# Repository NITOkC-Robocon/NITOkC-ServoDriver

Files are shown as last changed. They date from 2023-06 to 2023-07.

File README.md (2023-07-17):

# NITOkC-ServoDriver

## 概要
弊部独自のサーボドライバの回路データ、およびプログラムです<br>
(※デフォルトブランチ：main)

## 機能
- 2セルLiPoバッテリーからの給電
  - マイコンへの給電(電源切り離し機能付き)
  - サーボへの給電(レギュレータにより6Vに降圧)
- 中点指定機能
- 出力選択機能
- PWM幅可変機能
- 外部入力機能
  - 基板上のスライドスイッチによって切り替え可能

## 環境
| | |
| :-: | --- |
| OS | Windows 10 Pro |
| プログラム | Arm Keil Studio |
| 基板作成 | KiCad 7.0 |
| 使用マイコン | NUCLEO-F303K8 |
| 使用言語 | C++ |
| その他 | 弊部独自ライブラリの導入が必須(Privateリポジトリのため、今後依存関係を解消予定) |

## 開発者
[Resenaga_Byakko (Shogo Miyazato)](https://github.com/ByakkoMatsumiya)

## 連絡先
基板またはコードに関するお問い合わせは、[Issues](https://github.com/NITOkC-Robocon/NITOC-Robocon_HP/issues)または下記連絡先へお願い致します。
- [Twitter | @Seyanaga (趣味用アカウント)](https://twitter.com/Seyanaga)
- [Twitter | @Myaaaazato (ロボコン用アカウント)](https://twitter.com/Myaaaazato)

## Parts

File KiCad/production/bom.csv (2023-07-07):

Designator | Footprint | Quantity | Value | LCSC Part #
C1, C4 | CP_Radial_D8.0mm_P3.50mm | 2 | 100u
C2 | C_Disc_D3.4mm_W2.1mm_P2.50mm | 1 | 0.33u
C3 | C_Disc_D4.3mm_W1.9mm_P5.00mm | 1 | 0.1u
D1, D2 | D_DO-15_P10.16mm_Horizontal | 2 | PS2010R
D3 | LED_D3.0mm | 1 | SLR-332VC3F
D4 | LED_D3.0mm | 1 | SLR-332MC3F
D5 | LED_D3.0mm | 1 | SLR-332DC3F
D6 | LED_D3.0mm | 1 | SLR-332YC3F
J1 | Connector_T_Male | 1 | 2Cell
J2 | PinHeader_1x03_P2.54mm_Vertical | 1 | Servo_1
J3 | PinHeader_1x03_P2.54mm_Vertical | 1 | Servo_2
J4 | PinHeader_1x03_P2.54mm_Vertical | 1 | SIGNAL_INPUT
JP1 | PinHeader_1x02_P2.54mm_Vertical | 1 | VIN_BATT
R1, R2 | R_Axial_DIN0207_L6.3mm_D2.5mm_P10.16mm_Horizontal | 2 | 680
R3, R4, R5 | R_Axial_DIN0207_L6.3mm_D2.5mm_P10.16mm_Horizontal | 3 | 100
RV1 | Potentiometer_Alps_RK09K_Single_Vertical | 1 | 10k_B
SW1 | Slide_SS12D01Gx | 1 | PWM1_SW
SW2 | Slide_SS12D01Gx | 1 | PWM2_SW
SW3 | SW_PUSH_6mm | 1 | RST_SW
SW4 | SW_PUSH_6mm | 1 | CENTER_SW
SW5 | SW_PUSH_6mm | 1 | EN1_SW
SW6 | SW_PUSH_6mm | 1 | EN2_SW
U1 | TO-220-3_Vertical | 1 | LM7806_TO220
U2 | NUCLEO F303 K8 | 1 | NUCLEO_F303K8

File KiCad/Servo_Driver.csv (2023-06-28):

Source: | C:\Users\ic201239\Documents\KiCad\Servo_Controller\Servo_Controller.kicad_sch
Date: | 2023/05/24 18:18:11
Tool: | Eeschema 7.0.2
Generator: | C:\Program Files\KiCad\7.0\bin\scripting\plugins/bom_csv_grouped_by_value_with_fp.py
Component Count: | 29
Ref | Qnty | Value | Cmp name | Footprint | Description | Vendor | DNP
C1, C5 | 2 | 100u | C_Polarized_Small |  | Polarized capacitor, small symbol
C2, C4, C6, C7 | 4 | 0.1u | C_Small |  | Unpolarized capacitor, small symbol
C3 | 1 | 0.33u | C_Small |  | Unpolarized capacitor, small symbol
D1 | 1 | SLR-332VC3F | LED |  | Light emitting diode
D2 | 1 | SLR-332MC3F | LED |  | Light emitting diode
D3 | 1 | SLR-332DC3F | LED |  | Light emitting diode
D4 | 1 | SLR-332YC3F | LED |  | Light emitting diode
J1 | 1 | 2Cell | Conn_01x02_Pin |  | Generic connector, single row, 01x02, script generated
J2 | 1 | Servo_1 | Conn_01x03_Pin |  | Generic connector, single row, 01x03, script generated
J3 | 1 | Servo_2 | Conn_01x03_Pin |  | Generic connector, single row, 01x03, script generated
J4 | 1 | SIGNAL_INPUT | Conn_01x03_Pin |  | Generic connector, single row, 01x03, script generated
R1, R2 | 2 | 640 | R |  | Resistor
R3, R4, R5 | 3 | 100 | R |  | Resistor
RV1 | 1 | 10k_B | R_Potentiometer |  | Potentiometer
SW1 | 1 | CENTER_SW | SW_Push |  | Push button switch, generic, two pins
SW2 | 1 | RST_SW | SW_Push |  | Push button switch, generic, two pins
SW3 | 1 | EN1_SW | SW_Push |  | Push button switch, generic, two pins
SW4 | 1 | EN2_SW | SW_Push |  | Push button switch, generic, two pins
SW5 | 1 | PWM1_SW | SW_SPDT |  | Switch, single pole double throw
SW6 | 1 | PWM2_SW | SW_SPDT |  | Switch, single pole double throw
U1 | 1 | NUCLEO_F303K8 | NUCLEO_F303K8 | NUCLEO:NUCLEO F303 K8
U2 | 1 | LM7806_TO220 | LM7806_TO220 | Package_TO_SOT_THT:TO-220-3_Vertical | Positive 1A 35V Linear Regulator, Fixed Output 6V, TO-220

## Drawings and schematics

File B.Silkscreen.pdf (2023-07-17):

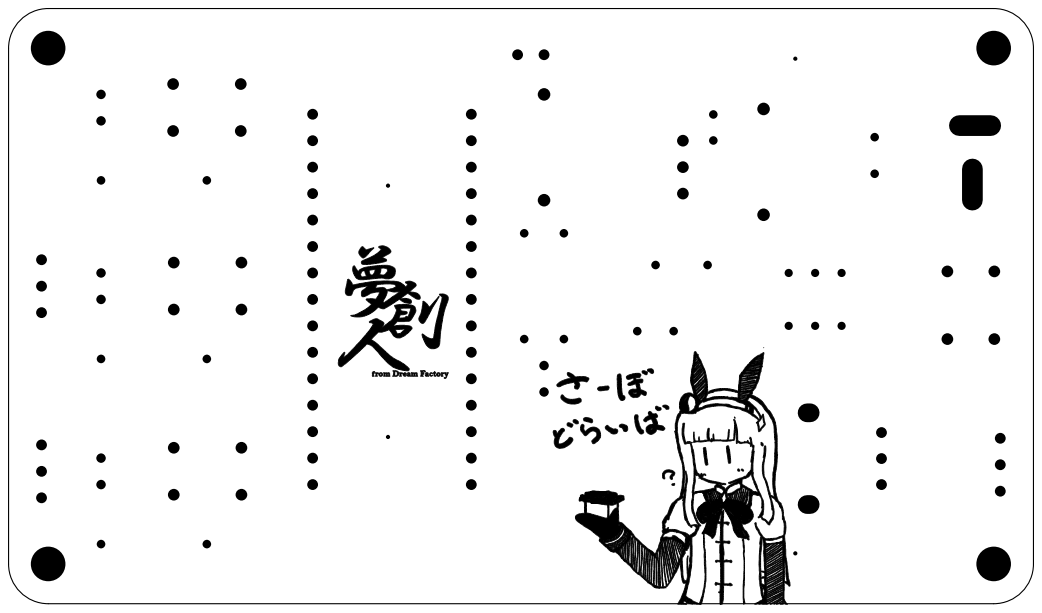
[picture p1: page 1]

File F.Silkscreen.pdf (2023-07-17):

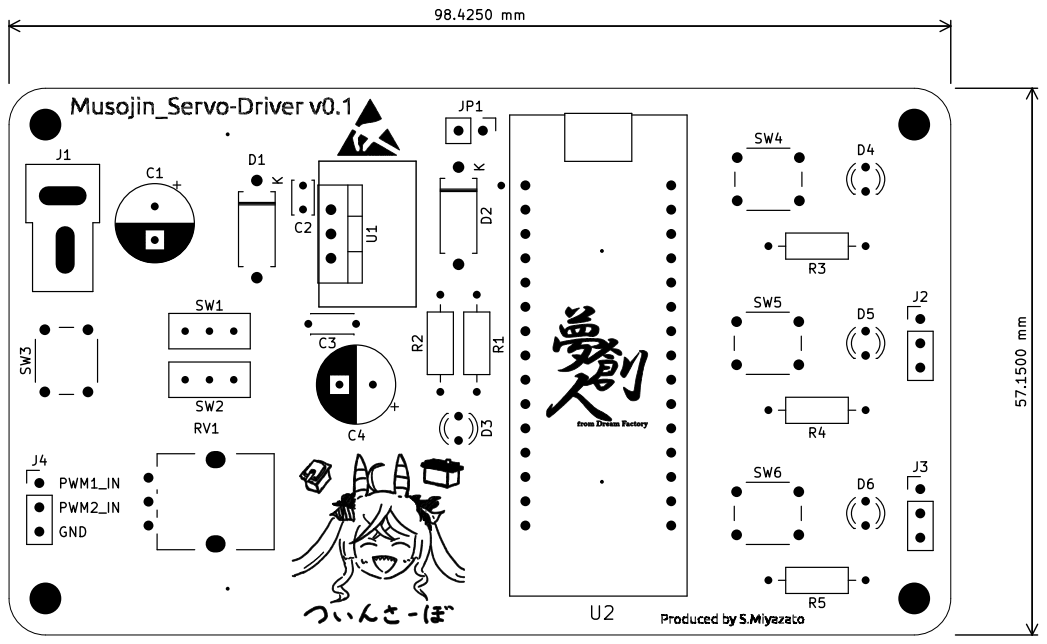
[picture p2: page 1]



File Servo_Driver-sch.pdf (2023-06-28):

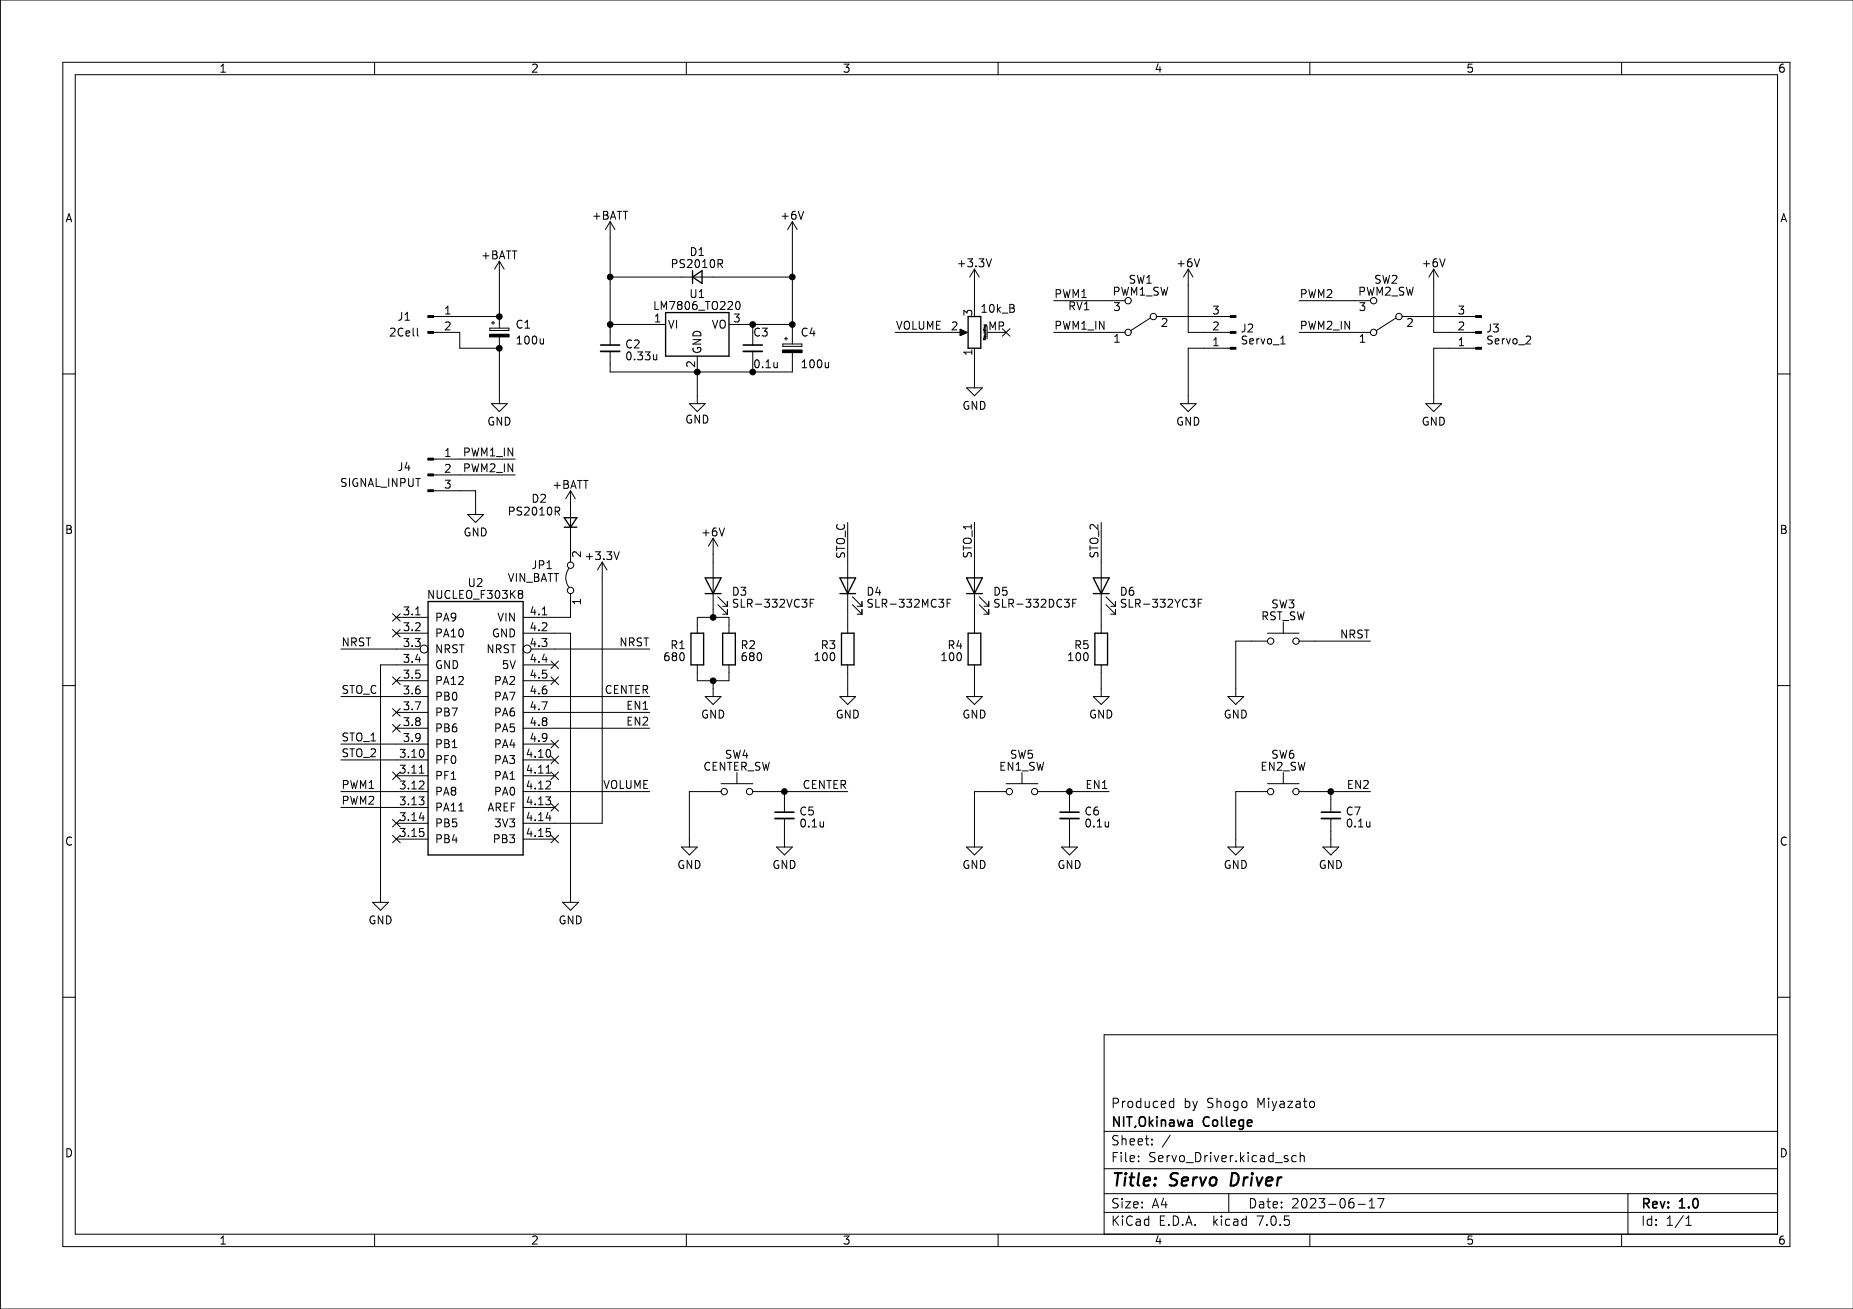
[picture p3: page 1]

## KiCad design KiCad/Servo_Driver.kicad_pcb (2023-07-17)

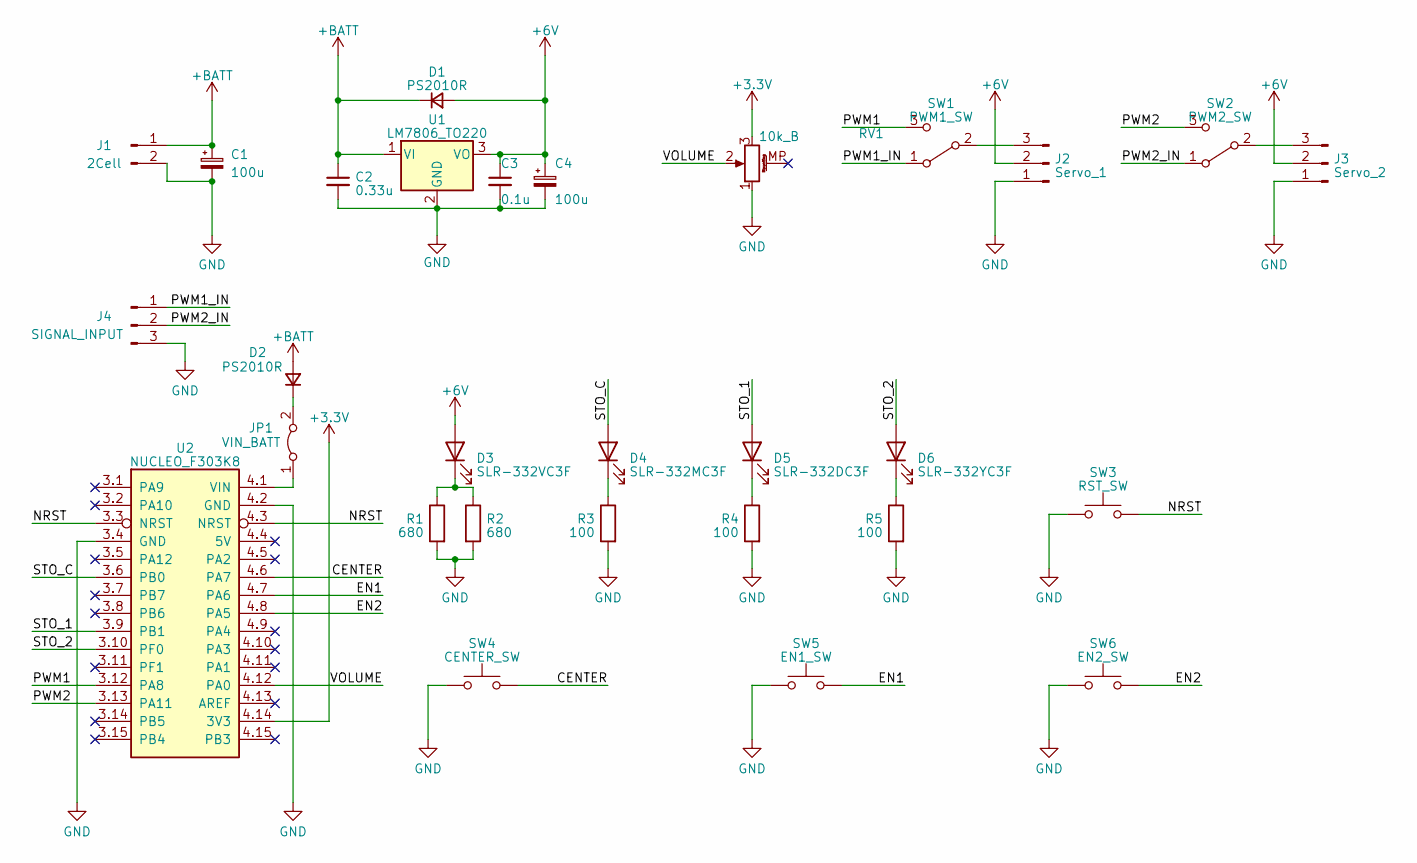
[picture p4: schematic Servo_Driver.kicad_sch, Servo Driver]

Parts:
C1, C4: 100u; CP_Radial_D8.0mm_P3.50mm
C2: 0.33u; C_Disc_D3.4mm_W2.1mm_P2.50mm
C3: 0.1u; C_Disc_D4.3mm_W1.9mm_P5.00mm
D1, D2: PS2010R; D_DO-15_P10.16mm_Horizontal
D3: SLR-332VC3F; LED_D3.0mm
D4: SLR-332MC3F; LED_D3.0mm
D5: SLR-332DC3F; LED_D3.0mm
D6: SLR-332YC3F; LED_D3.0mm
J1: 2Cell; Connector_T_Male
J2: Servo_1; PinHeader_1x03_P2.54mm_Vertical
J3: Servo_2; PinHeader_1x03_P2.54mm_Vertical
J4: SIGNAL_INPUT; PinHeader_1x03_P2.54mm_Vertical
JP1: VIN_BATT; PinHeader_1x02_P2.54mm_Vertical
R1, R2: 680; R_Axial_DIN0207_L6.3mm_D2.5mm_P10.16mm_Horizontal
R3, R4, R5: 100; R_Axial_DIN0207_L6.3mm_D2.5mm_P10.16mm_Horizontal
RV1: 10k_B; Potentiometer_Alps_RK09K_Single_Vertical
SW1: PWM1_SW; Slide_SS12D01Gx
SW2: PWM2_SW; Slide_SS12D01Gx
SW3: RST_SW; SW_PUSH_6mm
SW4: CENTER_SW; SW_PUSH_6mm
SW5: EN1_SW; SW_PUSH_6mm
SW6: EN2_SW; SW_PUSH_6mm
U1: LM7806_TO220; TO-220-3_Vertical
U2: NUCLEO_F303K8; NUCLEO F303 K8

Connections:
+3.3V: RV1.3, U2.4.14 (3V3)
+6V: C3.1, C4.1, D1.2 (A), D3.2 (A), J2.2, J3.2, U1.3 (VO)
+BATT: C1.1, C2.1, D1.1 (K), D2.2 (A), J1.1, U1.1 (VI)
/CENTER: SW4.2, U2.4.6 (PA7)
/EN1: SW5.2, U2.4.7 (PA6)
/EN2: SW6.2, U2.4.8 (PA5)
/NRST: SW3.2, U2.3.3 (NRST), U2.4.3 (NRST)
/PWM1: SW1.3 (C), U2.3.12 (PA8)
/PWM1_IN: J4.1, SW1.1 (A)
/PWM2: SW2.3 (C), U2.3.13 (PA11~)
/PWM2_IN: J4.2, SW2.1 (A)
/STO_1: D5.2 (A), U2.3.9 (PB1)
/STO_2: D6.2 (A), U2.3.10 (PF0)
/STO_C: D4.2 (A), U2.3.6 (PB0)
/VOLUME: RV1.2, U2.4.12 (PA0)
GND: C1.2, C2.2, C3.2, C4.2, J1.2, J2.1, J3.1, J4.3, R1.2, R2.2, R3.2, R4.2, R5.2, RV1.1, SW3.1, SW4.1, SW5.1, SW6.1, U1.2 (GND), U2.3.4 (GND), U2.4.2 (GND)
unnamed: D2.1 (K), JP1.2 (B)
unnamed: D3.1 (K), R1.1, R2.1
unnamed: D4.1 (K), R3.1
unnamed: D5.1 (K), R4.1
unnamed: D6.1 (K), R5.1
unnamed: J2.3, SW1.2 (B)
unnamed: J3.3, SW2.2 (B)
unnamed: JP1.1 (A), U2.4.1 (VIN)

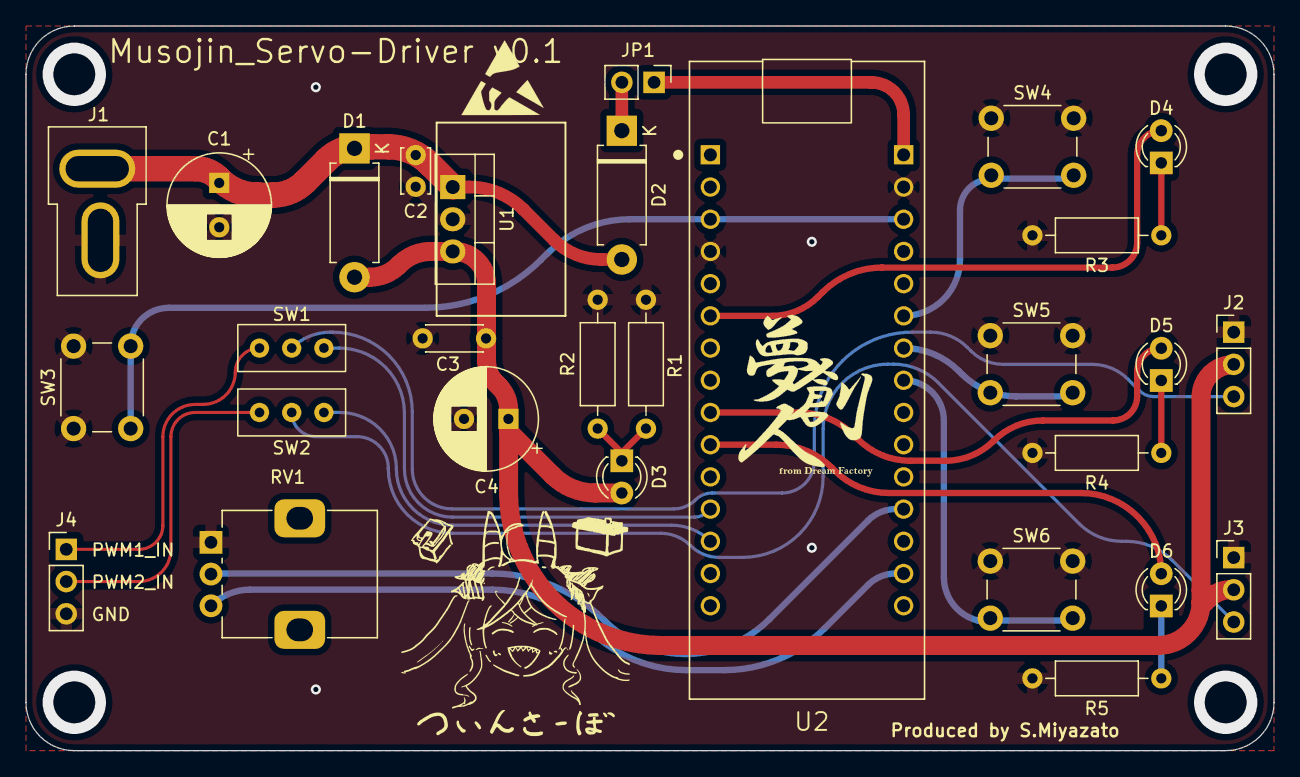
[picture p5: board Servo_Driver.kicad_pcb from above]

Board: 2 copper layers, 98.4 x 57.2 mm, 29 parts (0 on the bottom side), 24 nets.

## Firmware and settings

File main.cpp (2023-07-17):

#include "mbed.h"

DigitalOut STO_1 (PB_1);
DigitalOut STO_2 (PF_0);
DigitalOut STO_C (PB_0);

PwmOut PWM1 (PA_8);
PwmOut PWM2 (PA_11);

DigitalIn EN1 (PA_6);
DigitalIn EN2 (PA_5);
DigitalIn CENTER (PA_7);

AnalogIn VOLUME (PA_0);

void config(void);
void read_switches(void);
void set_pwm(void);
void set_led(void);

int EN1_OUT = 0;
int EN2_OUT = 0;
int CENTER_OUT = 1;

int VOLUME_OUT = 1500;

int main() {
    config();
    while(1) {
        read_switches();
        set_pwm();
        set_led();
        wait_ms(5);
    }
}

void config(void) {
    EN1.mode(PullUp);
    EN2.mode(PullUp);
    CENTER.mode(PullUp);
    PWM1.period_ms(20);
    PWM2.period_ms(20);
}

void read_switches(void) {
    int EN1_status = EN1.read();
    int EN2_status = EN2.read();
    int CENTER_status = CENTER.read();
    static int EN1_status_old;
    static int EN2_status_old;
    static int CENTER_status_old;
    double VOLUME_voltage = VOLUME.read();

    if(EN1_status_old == 1 && EN1_status == 0)
        EN1_OUT = !EN1_OUT;
    
    if(EN2_status_old == 1 && EN2_status == 0)
        EN2_OUT = !EN2_OUT;

    if(CENTER_status_old == 1 && CENTER_status == 0) {
        CENTER_OUT = !CENTER_OUT;
    }
    VOLUME_OUT = 500 + (int)(VOLUME_voltage * 2000.0);

    EN1_status_old = EN1_status;
    EN2_status_old = EN2_status;
    CENTER_status_old = CENTER_status;
}

void set_pwm(void) {
    if(EN1_OUT) {
        if(CENTER_OUT) {
            PWM1.pulsewidth_us(1500);
        }
        else {
            PWM1.pulsewidth_us(VOLUME_OUT);
        }
    }

    if(EN2_OUT) {
        if(CENTER_OUT) {
            PWM2.pulsewidth_us(1500);
        }
        else {
            PWM2.pulsewidth_us(VOLUME_OUT);
        }
    }
}

void set_led(void) {
    STO_1 = EN1_OUT;
    STO_2 = EN2_OUT;
    STO_C = CENTER_OUT;
}

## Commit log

2023-06-28 Upload kicad files.
    [Servo_Driver.csv, Servo_Driver.kicad_pcb, Servo_Driver.kicad_sch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]
2023-06-28 Change directory composition.
    [Servo_Driver.csv, Servo_Driver.kicad_pcb, Servo_Driver.kicad_sch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]
2023-06-28 ピン配置と関数分けを実施
2023-06-29 可変PWM幅制御の実装、LED点灯用の関数を追記
2023-06-29 出力切替機能の実装、中点SW押下時の挙動の修正
2023-07-07 基板を更新。部品配置の変更とフットプリントの配置
    [Servo_Driver.kicad_pcb, Servo_Driver.kicad_sch, bom.csv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]
2023-07-17 実機での動作確認に伴い不具合を修正
2023-07-17 基板にシルクスクリーンを追加、その他位置を微調整
    [Servo_Driver.kicad_pcb]
